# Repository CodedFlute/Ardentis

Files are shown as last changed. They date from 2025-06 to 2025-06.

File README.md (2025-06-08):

# Ardentis

> **⚠ WARNING:** This is currently a work in progress and untested. Only fly if you are willing and able to take full responsibility for any damage or property loss that may result from failure of this flight computer to operate as designed.

Ardentis is the best value high-performance flight computer designed specifically for high-power rocketry at all levels from 38mm min diameter to 132mm dual stage space shots.

This repository contains both the hardware and software required for Ardentis and its upgrades.

## Features

Ardentis comes in one default configurations, although any combination of features could be created by due to its open source design philosophy.

| Feature | Capability |
|-|-|
| Max Altitude | Baro: 25 km (85k ft) GPS: 80 km (250k ft) |
| GPS Tracking | Yes |
| Max Radio Range | ~15 km |
| Max Acceleration | 400G |
| Outputs | 4 (Servo + Air Start Capable) |
| Data Logging | MicroSD |
| Wi-Fi | Configuration and Control |

### Ardentis

<details>
<summary>Hardware Details</summary>

- **MCU**: ESP32-S3-MINI-1-N4R2
  - 4 MB Flash
  - 384 KB ROM
  - 512 KB SRAM
  - Dual core Xtense 32 bit LX7 at up to 240 MHz
- **Radio**: seeed studio SX126x Breakout
  - 22 dBm TX Power
  - 915 MHz ISM Band
  - u.Fl Antenna Connector
- **IMU**: ICM
  - +/- 16G Accelerometer
  - +/- 2000 Deg/s Gyroscope
- **High G Accelerometer**:
  - 3 Axis
  - +/- 100, 200, 400G Ranges
- **Barometer**: MS5611
  - 10 cm Resolution
  - 10 mBar to 1 200 mBar Operating Range
- **GPS**: uBlox SAM-M10Q
  - 80 km (250k ft) Max Altitude
  - 500 m/s (1.45 Mach) Max Velocity
  - 4G Max Acceleration
- **Ignition Channels**4
- **Connectivity**: Bluetooth 5.0, Wi-Fi, Micro USB
- **Power**: 1S LiPo battery support (or anything between 2V and 5V)

</details>

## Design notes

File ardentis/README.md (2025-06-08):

# Hardware

This folder contains the KiCAD files for the Ardentis hardware. These were made using KiCAD 9.0.

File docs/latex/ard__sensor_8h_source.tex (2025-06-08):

\doxysection{ard\+\_\+sensor.\+h}
\hypertarget{ard__sensor_8h_source}{}\label{ard__sensor_8h_source}\index{main/ard\_sensor.h@{main/ard\_sensor.h}}

\begin{DoxyCode}{0}
\DoxyCodeLine{00001\ \textcolor{preprocessor}{\#pragma\ once}}
\DoxyCodeLine{00002\ }
\DoxyCodeLine{00003\ \textcolor{preprocessor}{\#include\ <stdint.h>}}
\DoxyCodeLine{00004\ }
\DoxyCodeLine{00005\ \textcolor{preprocessor}{\#include\ <SparkFun\_u-\/blox\_GNSS\_v3.h>}}
\DoxyCodeLine{00006\ }
\DoxyCodeLine{00007\ \textcolor{preprocessor}{\#include\ <Adafruit\_Sensor.h>}\ \textcolor{comment}{//Needed\ for\ adafruit\ sensor\ libraries}}
\DoxyCodeLine{00008\ \textcolor{preprocessor}{\#include\ <Adafruit\_H3LIS331.h>}\ \textcolor{comment}{//\ For\ H3LIS331\ High\ G\ Accelerometer}}
\DoxyCodeLine{00009\ }
\DoxyCodeLine{00010\ \textcolor{preprocessor}{\#include\ <ICM42670P.h>}\ \textcolor{comment}{//\ For\ ICM42670P\ IMU}}
\DoxyCodeLine{00011\ }
\DoxyCodeLine{00012\ \textcolor{preprocessor}{\#include\ <icm42670.h>}}
\DoxyCodeLine{00013\ }
\DoxyCodeLine{00014\ \textcolor{preprocessor}{\#include\ <MS5611.h>}\ \textcolor{comment}{//\ For\ MS5611\ Barometer}}
\DoxyCodeLine{00015\ }
\DoxyCodeLine{00016\ \textcolor{preprocessor}{\#include\ <Wire.h>}\ \textcolor{comment}{//\ For\ I2C\ communication}}
\DoxyCodeLine{00017\ }
\DoxyCodeLine{00018\ \textcolor{preprocessor}{\#include\ <HardwareSerial.h>}}
\DoxyCodeLine{00019\ }
\DoxyCodeLine{00020\ \textcolor{preprocessor}{\#include\ <driver/i2c\_master.h>}}
\DoxyCodeLine{00027\ \textcolor{keyword}{struct\ }\mbox{\hyperlink{structard_data_field}{ardDataField}}\ \{}
\DoxyCodeLine{00028\ \ \ \ \ int16\_t\ val;}
\DoxyCodeLine{00029\ \ \ \ \ int64\_t\ timestamp;}
\DoxyCodeLine{00030\ \ \ \ \ \textcolor{keywordtype}{bool}\ updated;}
\DoxyCodeLine{00031\ \};}
\DoxyCodeLine{00037\ \textcolor{keywordtype}{void}\ updateArdDataField(\mbox{\hyperlink{structard_data_field}{ardDataField}}*\ field,\ int16\_t\ val);}
\DoxyCodeLine{00038\ }
\DoxyCodeLine{00048\ \textcolor{keyword}{class\ }ardSensors\ \{}
\DoxyCodeLine{00049\ \textcolor{keyword}{public}:}
\DoxyCodeLine{00050\ \ \ \ \ ardSensors(gpio\_num\_t\ sda,\ gpio\_num\_t\ scl,\ \textcolor{keywordtype}{int}\ i2c,\ \textcolor{keywordtype}{int}\ gps\_uart\_num,\ gpio\_num\_t\ gps\_tx,\ gpio\_num\_t\ gps\_rx);}
\DoxyCodeLine{00051\ \ \ \ \ \string~ardSensors();}
\DoxyCodeLine{00052\ }
\DoxyCodeLine{00061\ \ \ \ \ esp\_err\_t\ \mbox{\hyperlink{classard_sensors_af8da5ef8f7232141c86709f8613ad1a3}{initSensors}}(\textcolor{keywordtype}{int}\ LIS331\_addr,\ \textcolor{keywordtype}{int}\ imu\_adr,\ \textcolor{keywordtype}{int}\ baro\_addr,\ \textcolor{keywordtype}{int}\ gps\_baud);}
\DoxyCodeLine{00062\ \ \ \ \ esp\_err\_t\ update();\ \textcolor{comment}{//\ Function\ to\ check\ if\ new\ sensor\ data\ is\ available\ and\ update\ the\ data\ fields\ accordingly.}}
\DoxyCodeLine{00063\ \ \ \ \ \mbox{\hyperlink{structard_data_field}{ardDataField}}\ accelX;\ \textcolor{comment}{//\ Accelerometer\ X-\/axis\ data}}
\DoxyCodeLine{00064\ \ \ \ \ \mbox{\hyperlink{structard_data_field}{ardDataField}}\ accelY;\ \textcolor{comment}{//\ Accelerometer\ Y-\/axis\ data}}
\DoxyCodeLine{00065\ \ \ \ \ \mbox{\hyperlink{structard_data_field}{ardDataField}}\ accelZ;\ \textcolor{comment}{//\ Accelerometer\ Z-\/axis\ data}}
\DoxyCodeLine{00066\ \ \ \ \ \mbox{\hyperlink{structard_data_field}{ardDataField}}\ gyroX;\ \textcolor{comment}{//\ Gyroscope\ X-\/axis\ data}}
\DoxyCodeLine{00067\ \ \ \ \ \mbox{\hyperlink{structard_data_field}{ardDataField}}\ gyroY;\ \textcolor{comment}{//\ Gyroscope\ Y-\/axis\ data}}
\DoxyCodeLine{00068\ \ \ \ \ \mbox{\hyperlink{structard_data_field}{ardDataField}}\ gyroZ;\ \textcolor{comment}{//\ Gyroscope\ Y-\/axis\ data}}
\DoxyCodeLine{00069\ \ \ \ \ \mbox{\hyperlink{structard_data_field}{ardDataField}}\ highAccelX;\ \textcolor{comment}{//\ High\ G\ Accelerometer\ X-\/axis\ data}}
\DoxyCodeLine{00070\ \ \ \ \ \mbox{\hyperlink{structard_data_field}{ardDataField}}\ highAccelY;\ \textcolor{comment}{//\ High\ G\ Accelerometer\ Y-\/axis\ data}}
\DoxyCodeLine{00071\ \ \ \ \ \mbox{\hyperlink{structard_data_field}{ardDataField}}\ highAccelZ;\ \textcolor{comment}{//\ High\ G\ Accelerometer\ Z-\/axis\ data}}
\DoxyCodeLine{00072\ \ \ \ \ \mbox{\hyperlink{structard_data_field}{ardDataField}}\ pressure;\ \textcolor{comment}{//\ Pressure\ data\ from\ barometer}}
\DoxyCodeLine{00073\ \ \ \ \ \mbox{\hyperlink{structard_data_field}{ardDataField}}\ altitude;\ \textcolor{comment}{//\ Altitude\ data\ from\ barometer}}
\DoxyCodeLine{00074\ \ \ \ \ \mbox{\hyperlink{structard_data_field}{ardDataField}}\ temperature;\ \textcolor{comment}{//\ Temperature\ data\ from\ barometer}}
\DoxyCodeLine{00075\ \ \ \ \ \mbox{\hyperlink{structard_data_field}{ardDataField}}\ latitude;\ \textcolor{comment}{//\ Latitude\ data\ from\ GPS}}
\DoxyCodeLine{00076\ \ \ \ \ \mbox{\hyperlink{structard_data_field}{ardDataField}}\ longitude;\ \textcolor{comment}{//\ Longitude\ data\ from\ GPS}}
\DoxyCodeLine{00077\ \ \ \ \ \mbox{\hyperlink{structard_data_field}{ardDataField}}\ horizAccuracy;\ \textcolor{comment}{//\ Horizontal\ accuracy\ from\ GPS}}
\DoxyCodeLine{00078\ \ \ \ \ \mbox{\hyperlink{structard_data_field}{ardDataField}}\ vertAccuracy;\ \textcolor{comment}{//\ Vertical\ accuracy\ from\ GPS}}
\DoxyCodeLine{00079\ \ \ \ \ \mbox{\hyperlink{structard_data_field}{ardDataField}}\ gps\_altitude;\ \textcolor{comment}{//\ Altitude\ data\ from\ GPS}}
\DoxyCodeLine{00080\ \textcolor{keyword}{private}:}
\DoxyCodeLine{00081\ \ \ \ \ TwoWire\ ard\_sensor\_i2c\ =\ NULL;\ \textcolor{comment}{//\ Arduino\ I2C\ bus\ object}}
\DoxyCodeLine{00082\ \ \ \ \ SFE\_UBLOX\_GNSS\_SERIAL\ gps;\ \textcolor{comment}{//\ GPS\ object}}
\DoxyCodeLine{00083\ \ \ \ \ HardwareSerial\ gps\_uart\ =\ NULL;\ \textcolor{comment}{//\ GPS\ UART\ bus\ object}}
\DoxyCodeLine{00084\ \ \ \ \ MS5611\ barometer;\ \textcolor{comment}{//\ Barometer\ object}}
\DoxyCodeLine{00085\ \ \ \ \ Adafruit\_H3LIS331\ accel\ =\ Adafruit\_H3LIS331();\ \textcolor{comment}{//\ High\ G\ Accelerometer\ object}}
\DoxyCodeLine{00086\ \ \ \ \ icm42670\_handle\_t\ imu\_handle\ =\ \textcolor{keyword}{nullptr};\ \textcolor{comment}{//\ ICM42670\ IMU\ object}}
\DoxyCodeLine{00087\ \ \ \ \ i2c\_master\_bus\_handle\_t\ i2c\_handle\ =\ NULL;\ \textcolor{comment}{//\ ESP-\/IDF\ I2C\ bus\ object}}
\DoxyCodeLine{00088\ \ \ \ \ gpio\_num\_t\ sda;\ \textcolor{comment}{//\ SDA\ GPIO\ pin}}
\DoxyCodeLine{00089\ \ \ \ \ gpio\_num\_t\ scl;\ \textcolor{comment}{//\ SCL\ GPIO\ pin}}
\DoxyCodeLine{00090\ \ \ \ \ gpio\_num\_t\ uart\_rx;\ \textcolor{comment}{//\ GPS\ RX\ GPIO\ pin}}
\DoxyCodeLine{00091\ \ \ \ \ gpio\_num\_t\ uart\_tx;\ \textcolor{comment}{//\ GPS\ TX\ GPIO\ pin}}
\DoxyCodeLine{00092\ \ \ \ \ \textcolor{keywordtype}{int}\ gps\_uart\_num;\ \textcolor{comment}{//\ GPS\ UART\ bus\ number}}
\DoxyCodeLine{00093\ \ \ \ \ \textcolor{keywordtype}{int}\ i2c\_num;\ \textcolor{comment}{//\ I2C\ bus\ number}}
\DoxyCodeLine{00094\ \ \ \ \ int16\_t\ imu\_update\_time;\ \textcolor{comment}{//\ Timestamp\ of\ the\ last\ IMU\ update}}
\DoxyCodeLine{00095\ \ \ \ \ int16\_t\ imu\_update\_interval;\ \textcolor{comment}{//\ Interval\ between\ IMU\ updates\ in\ microseconds}}
\DoxyCodeLine{00096\ \ \ \ \ int16\_t\ high\_g\_accel\_update\_time;\ \textcolor{comment}{//\ Timestamp\ of\ the\ last\ High\ G\ Accelerometer\ update}}
\DoxyCodeLine{00097\ \ \ \ \ int16\_t\ high\_g\_accel\_update\_interval;\ \textcolor{comment}{//\ Interval\ between\ High\ G\ Accelerometer\ updates\ in\ microseconds}}
\DoxyCodeLine{00098\ \ \ \ \ int16\_t\ barometer\_update\_time;\ \textcolor{comment}{//\ Timestamp\ of\ the\ last\ Barometer\ update}}
\DoxyCodeLine{00099\ \ \ \ \ int16\_t\ barometer\_update\_interval;\ \textcolor{comment}{//\ Interval\ between\ Barometer\ updates\ in\ microseconds}}
\DoxyCodeLine{00100\ \ \ \ \ int16\_t\ gps\_update\_time;\ \textcolor{comment}{//\ Timestamp\ of\ the\ last\ GPS\ update}}
\DoxyCodeLine{00101\ \ \ \ \ int16\_t\ gps\_update\_interval;\ \textcolor{comment}{//\ Interval\ between\ GPS\ updates\ in\ microseconds}}
\DoxyCodeLine{00102\ \};}

\end{DoxyCode}

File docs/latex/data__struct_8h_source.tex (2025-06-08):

\doxysection{data\+\_\+struct.\+h}
\hypertarget{data__struct_8h_source}{}\label{data__struct_8h_source}\index{main/data\_struct.h@{main/data\_struct.h}}

\begin{DoxyCode}{0}
\DoxyCodeLine{00001\ \textcolor{preprocessor}{\#pragma\ once}}
\DoxyCodeLine{00002\ }
\DoxyCodeLine{00003\ \textcolor{preprocessor}{\#include\ <Arduino.h>}}
\DoxyCodeLine{00004\ }
\DoxyCodeLine{00005\ \textcolor{keyword}{struct\ }\mbox{\hyperlink{struct_ard_data_struct}{ArdDataStruct}}\ \{}
\DoxyCodeLine{00006\ \ \ \ \ uint16\_t\ pressure;}
\DoxyCodeLine{00007\ \ \ \ \ int32\_t\ latitude;}
\DoxyCodeLine{00008\ \ \ \ \ int32\_t\ longitude;}
\DoxyCodeLine{00009\ \ \ \ \ int16\_t\ horizAccuracy;}
\DoxyCodeLine{00010\ \ \ \ \ int16\_t\ vertAccuracy;}
\DoxyCodeLine{00011\ \ \ \ \ int16\_t\ temperature;}
\DoxyCodeLine{00012\ \ \ \ \ int16\_t\ accelX;}
\DoxyCodeLine{00013\ \ \ \ \ int16\_t\ accelY;}
\DoxyCodeLine{00014\ \ \ \ \ int16\_t\ accelZ;}
\DoxyCodeLine{00015\ \ \ \ \ int16\_t\ highAccelX;}
\DoxyCodeLine{00016\ \ \ \ \ int16\_t\ highAccelY;}
\DoxyCodeLine{00017\ \ \ \ \ int16\_t\ highAccelZ;}
\DoxyCodeLine{00018\ \ \ \ \ int16\_t\ gyroX;}
\DoxyCodeLine{00019\ \ \ \ \ int16\_t\ gyroY;}
\DoxyCodeLine{00020\ \ \ \ \ int16\_t\ gyroZ;}
\DoxyCodeLine{00021\ \ \ \ \ int16\_t\ altitude;}
\DoxyCodeLine{00022\ \ \ \ \ \textcolor{keywordtype}{bool}\ cont1;}
\DoxyCodeLine{00023\ \ \ \ \ \textcolor{keywordtype}{bool}\ cont2;}
\DoxyCodeLine{00024\ \ \ \ \ \textcolor{keywordtype}{bool}\ cont3;}
\DoxyCodeLine{00025\ \ \ \ \ \textcolor{keywordtype}{bool}\ cont4;}
\DoxyCodeLine{00026\ \ \ \ \ \textcolor{keywordtype}{bool}\ fired\_1;}
\DoxyCodeLine{00027\ \ \ \ \ \textcolor{keywordtype}{bool}\ fired\_2;}
\DoxyCodeLine{00028\ \ \ \ \ \textcolor{keywordtype}{bool}\ fired\_3;}
\DoxyCodeLine{00029\ \ \ \ \ \textcolor{keywordtype}{bool}\ fired\_4;}
\DoxyCodeLine{00030\ }
\DoxyCodeLine{00031\ \ \ \ \ uint16\_t\ getAltitude(\textcolor{keywordtype}{int}\ sea\_pressure)\textcolor{keyword}{\ const\ }\{}
\DoxyCodeLine{00032\ \ \ \ \ \ \ \ \ \textcolor{comment}{//\ Example\ calculation\ for\ altitude\ based\ on\ pressure}}
\DoxyCodeLine{00033\ \ \ \ \ \ \ \ \ \textcolor{comment}{//\ Replace\ with\ your\ actual\ formula}}
\DoxyCodeLine{00034\ \ \ \ \ \ \ \ \ \textcolor{keywordflow}{return}\ ((pow((sea\_pressure\ /\ pressure),\ 1/5.257)\ -\/\ 1.0)\ *\ (temperature\ +\ 273.15))\ /\ 0.0065;}
\DoxyCodeLine{00035\ \ \ \ \ \}}
\DoxyCodeLine{00036\ \};}

\end{DoxyCode}

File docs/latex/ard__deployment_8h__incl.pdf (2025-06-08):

main/ard_deployment.h

driver/gpio.h | esp_err.h | esp_log.h

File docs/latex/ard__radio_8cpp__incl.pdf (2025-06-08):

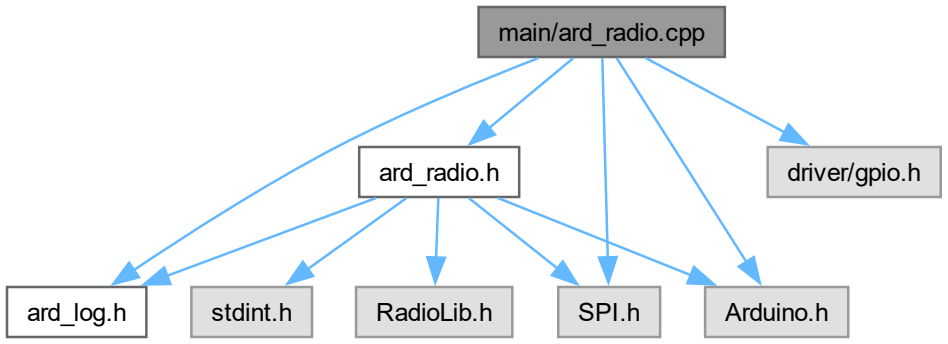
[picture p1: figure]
main/ard_radio.cpp; ard_radio.h; ard_log.h; SPI.h; Arduino.h; driver/gpio.h; stdint.h; RadioLib.h

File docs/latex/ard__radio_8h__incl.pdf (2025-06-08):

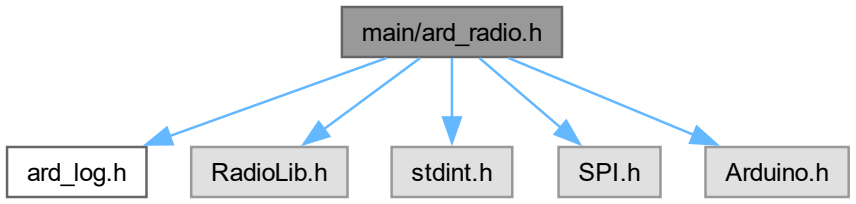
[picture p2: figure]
main/ard_radio.h; ard_log.h; RadioLib.h; stdint.h; SPI.h; Arduino.h

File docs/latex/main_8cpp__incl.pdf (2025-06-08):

main/main.cpp

pins.h

fire_modes.hpp | RadioParameters.h | ard_radio.h
ard_log.h | Arduino.h
data_struct.h | ard_deployment.h

Wire.h

FS.h | LittleFS.h | SD.h | Preferences.h | ard_sensor.h
RadioLib.h | SPI.h | driver/gpio.h | stdint.h | esp_err.h | esp_log.h | HardwareSerial.h | driver/i2c_master.h | SparkFun_u-blox_GNSS_v3.h | Adafruit_Sensor.h | Adafruit_H3LIS331.h | ICM42670P.h | icm42670.h | MS5611.h

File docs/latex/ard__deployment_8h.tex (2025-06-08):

\doxysection{main/ard\+\_\+deployment.h File Reference}
\hypertarget{ard__deployment_8h}{}\label{ard__deployment_8h}\index{main/ard\_deployment.h@{main/ard\_deployment.h}}

Header file for the ard\+\_\+deployment class.  

{\ttfamily \#include $<$driver/gpio.\+h$>$}\newline
{\ttfamily \#include $<$esp\+\_\+err.\+h$>$}\newline
{\ttfamily \#include $<$esp\+\_\+log.\+h$>$}\newline
Include dependency graph for ard\+\_\+deployment.\+h\+:\nopagebreak
\begin{figure}[H]
\begin{center}
\leavevmode

\end{center}
\end{figure}
This graph shows which files directly or indirectly include this file\+:\nopagebreak
\begin{figure}[H]
\begin{center}
\leavevmode

\end{center}
\end{figure}
\doxysubsubsection*{Classes}
\begin{DoxyCompactItemize}
\item 
struct \mbox{\hyperlink{structard_deploy_gpio_config}{ard\+Deploy\+Gpio\+Config}}
\begin{DoxyCompactList}\small\item\em Configuration structure for GPIO pins used in deployment. \end{DoxyCompactList}\item 
class \mbox{\hyperlink{classard_output_g_p_i_o}{ard\+Output\+GPIO}}
\begin{DoxyCompactList}\small\item\em Class to manage GPIO pins for deployment. \end{DoxyCompactList}\end{DoxyCompactItemize}
\doxysubsubsection*{Enumerations}
\begin{DoxyCompactItemize}
\item 
enum class \mbox{\hyperlink{ard__deployment_8h_a0d5bf0014cb0a1f121b08aef183dffc5}{Fire\+Pins}} \+: uint8\+\_\+t \{ {\bfseries Zero} = 0
, {\bfseries One} = 1
, {\bfseries Two} = 2
, {\bfseries Three} = 3
 \}
\begin{DoxyCompactList}\small\item\em Enum containing the valid fire indices. \end{DoxyCompactList}\end{DoxyCompactItemize}

\doxysubsection{Detailed Description}
Header file for the ard\+\_\+deployment class. 

\begin{DoxyAuthor}{Author}
Roland Neill 
\end{DoxyAuthor}
\begin{DoxyVersion}{Version}
0.\+1 
\end{DoxyVersion}
\begin{DoxyDate}{Date}
2025-\/04-\/25
\end{DoxyDate}
\begin{DoxyCopyright}{Copyright}
Copyright (c) 2025
\end{DoxyCopyright}
This file contains the definition of the ard\+\_\+deployment class, which is used to manage GPIO pins for deployment purposes. 

\doxysubsection{Enumeration Type Documentation}
\Hypertarget{ard__deployment_8h_a0d5bf0014cb0a1f121b08aef183dffc5}\index{ard\_deployment.h@{ard\_deployment.h}!FirePins@{FirePins}}
\index{FirePins@{FirePins}!ard\_deployment.h@{ard\_deployment.h}}
\doxysubsubsection{\texorpdfstring{FirePins}{FirePins}}
{\footnotesize\ttfamily \label{ard__deployment_8h_a0d5bf0014cb0a1f121b08aef183dffc5} 
enum class \mbox{\hyperlink{ard__deployment_8h_a0d5bf0014cb0a1f121b08aef183dffc5}{Fire\+Pins}} \+: uint8\+\_\+t\hspace{0.3cm}{\ttfamily [strong]}}

Enum containing the valid fire indices. 

\begin{DoxyCode}{0}
\DoxyCodeLine{00037\ \ \ \ \ \ \ \ \ \ \ \ \ \ \ \ \ \ \ \ \ :\ uint8\_t\ \{}
\DoxyCodeLine{00038\ \ \ \ \ Zero\ =\ 0,}
\DoxyCodeLine{00039\ \ \ \ \ One\ =\ 1,}
\DoxyCodeLine{00040\ \ \ \ \ Two\ =\ 2,}
\DoxyCodeLine{00041\ \ \ \ \ Three\ =\ 3}
\DoxyCodeLine{00042\ \};}

\end{DoxyCode}

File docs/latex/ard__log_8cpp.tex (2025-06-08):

\doxysection{main/ard\+\_\+log.cpp File Reference}
\hypertarget{ard__log_8cpp}{}\label{ard__log_8cpp}\index{main/ard\_log.cpp@{main/ard\_log.cpp}}

Logging library implementation for the Ardentis flight computer.  

{\ttfamily \#include "{}ard\+\_\+log.\+h"{}}\newline
{\ttfamily \#include $<$esp\+\_\+log.\+h$>$}\newline
Include dependency graph for ard\+\_\+log.\+cpp\+:
\nopagebreak
\begin{figure}[H]
\begin{center}
\leavevmode

\end{center}
\end{figure}

\doxysubsection{Detailed Description}
Logging library implementation for the Ardentis flight computer. 

\begin{DoxyAuthor}{Author}
Roland Neill 
\end{DoxyAuthor}
\begin{DoxyVersion}{Version}
0.\+1-\/alpha 
\end{DoxyVersion}
\begin{DoxyDate}{Date}
2025-\/04-\/28
\end{DoxyDate}
\begin{DoxyCopyright}{Copyright}
Copyright (c) 2025 
\end{DoxyCopyright}

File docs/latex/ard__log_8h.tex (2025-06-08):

\doxysection{main/ard\+\_\+log.h File Reference}
\hypertarget{ard__log_8h}{}\label{ard__log_8h}\index{main/ard\_log.h@{main/ard\_log.h}}

Logging library header for the Ardentis flight computer.  

This graph shows which files directly or indirectly include this file\+:
\nopagebreak
\begin{figure}[H]
\begin{center}
\leavevmode
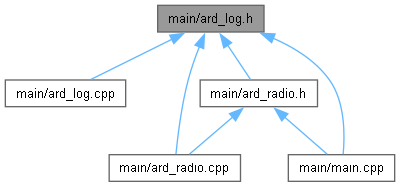
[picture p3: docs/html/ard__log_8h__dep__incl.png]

\end{center}
\end{figure}
\doxysubsubsection*{Classes}
\begin{DoxyCompactItemize}
\item 
class \mbox{\hyperlink{classard_log}{ard\+Log}}
\end{DoxyCompactItemize}
\doxysubsubsection*{Enumerations}
\begin{DoxyCompactItemize}
\item 
enum \mbox{\hyperlink{ard__log_8h_a2bcec6abac24273ae7d38f257f7d41b4}{ard\+\_\+log\+Level\+\_\+t}} \{ \newline
{\bfseries LOG\+\_\+\+DISABLE} = 0
, {\bfseries LOG\+\_\+\+ERROR} = 1
, {\bfseries LOG\+\_\+\+WARN} = 2
, {\bfseries LOG\+\_\+\+INFO} = 3
, \newline
{\bfseries LOG\+\_\+\+DEBUG} = 4
, {\bfseries LOG\+\_\+\+VERBOSE} = 5
 \}
\begin{DoxyCompactList}\small\item\em Logging level enum type. \end{DoxyCompactList}\item 
enum \mbox{\hyperlink{ard__log_8h_ab24eeb30e1bc9136bb3054df8c6e1470}{ard\+\_\+error\+Code\+\_\+t}} \{ {\bfseries ERROR\+\_\+\+NONE} = 0
, {\bfseries ERROR\+\_\+\+GENERIC} = -\/1
 \}
\begin{DoxyCompactList}\small\item\em Enumeration type for error codes. \end{DoxyCompactList}\end{DoxyCompactItemize}

\doxysubsection{Detailed Description}
Logging library header for the Ardentis flight computer. 

\begin{DoxyAuthor}{Author}
Roland Neill 
\end{DoxyAuthor}
\begin{DoxyVersion}{Version}
0.\+1-\/alpha 
\end{DoxyVersion}
\begin{DoxyDate}{Date}
2025-\/04-\/28
\end{DoxyDate}
\begin{DoxyCopyright}{Copyright}
Copyright (c) 2025 
\end{DoxyCopyright}

\doxysubsection{Enumeration Type Documentation}
\Hypertarget{ard__log_8h_ab24eeb30e1bc9136bb3054df8c6e1470}\index{ard\_log.h@{ard\_log.h}!ard\_errorCode\_t@{ard\_errorCode\_t}}
\index{ard\_errorCode\_t@{ard\_errorCode\_t}!ard\_log.h@{ard\_log.h}}
\doxysubsubsection{\texorpdfstring{ard\_errorCode\_t}{ard\_errorCode\_t}}
{\footnotesize\ttfamily \label{ard__log_8h_ab24eeb30e1bc9136bb3054df8c6e1470} 
enum \mbox{\hyperlink{ard__log_8h_ab24eeb30e1bc9136bb3054df8c6e1470}{ard\+\_\+error\+Code\+\_\+t}}}

Enumeration type for error codes. 

\begin{DoxyCode}{0}
\DoxyCodeLine{00030\ \ \ \ \ \ \ \ \ \ \ \ \ \ \ \ \ \ \ \ \ \ \{}
\DoxyCodeLine{00031\ \ \ \ \ ERROR\_NONE\ =\ 0,}
\DoxyCodeLine{00032\ \ \ \ \ ERROR\_GENERIC\ =\ -\/1}
\DoxyCodeLine{00033\ \};}

\end{DoxyCode}
\Hypertarget{ard__log_8h_a2bcec6abac24273ae7d38f257f7d41b4}\index{ard\_log.h@{ard\_log.h}!ard\_logLevel\_t@{ard\_logLevel\_t}}
\index{ard\_logLevel\_t@{ard\_logLevel\_t}!ard\_log.h@{ard\_log.h}}
\doxysubsubsection{\texorpdfstring{ard\_logLevel\_t}{ard\_logLevel\_t}}
{\footnotesize\ttfamily \label{ard__log_8h_a2bcec6abac24273ae7d38f257f7d41b4} 
enum \mbox{\hyperlink{ard__log_8h_a2bcec6abac24273ae7d38f257f7d41b4}{ard\+\_\+log\+Level\+\_\+t}}}

Logging level enum type. 

\begin{DoxyCode}{0}
\DoxyCodeLine{00017\ \ \ \ \ \ \ \ \ \ \ \ \ \ \ \ \ \ \ \ \ \{}
\DoxyCodeLine{00018\ \ \ \ \ LOG\_DISABLE\ =\ 0,}
\DoxyCodeLine{00019\ \ \ \ \ LOG\_ERROR\ =\ 1,}
\DoxyCodeLine{00020\ \ \ \ \ LOG\_WARN\ =\ 2,}
\DoxyCodeLine{00021\ \ \ \ \ LOG\_INFO\ =\ 3,}
\DoxyCodeLine{00022\ \ \ \ \ LOG\_DEBUG\ =\ 4,}
\DoxyCodeLine{00023\ \ \ \ \ LOG\_VERBOSE\ =\ 5}
\DoxyCodeLine{00024\ \};}

\end{DoxyCode}

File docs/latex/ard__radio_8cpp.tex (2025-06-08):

\doxysection{main/ard\+\_\+radio.cpp File Reference}
\hypertarget{ard__radio_8cpp}{}\label{ard__radio_8cpp}\index{main/ard\_radio.cpp@{main/ard\_radio.cpp}}

Implementation code for the radio module for the Ardentis flight computer.  

{\ttfamily \#include "{}ard\+\_\+radio.\+h"{}}\newline
{\ttfamily \#include "{}ard\+\_\+log.\+h"{}}\newline
{\ttfamily \#include "{}driver/gpio.\+h"{}}\newline
{\ttfamily \#include $<$Arduino.\+h$>$}\newline
{\ttfamily \#include $<$SPI.\+h$>$}\newline
Include dependency graph for ard\+\_\+radio.\+cpp\+:
\nopagebreak
\begin{figure}[H]
\begin{center}
\leavevmode
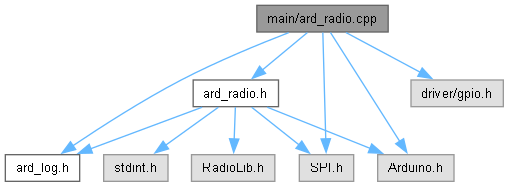
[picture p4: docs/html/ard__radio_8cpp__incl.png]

\end{center}
\end{figure}
\doxysubsubsection*{Functions}
\begin{DoxyCompactItemize}
\item 
byte \texorpdfstring{$\ast$}{*} \mbox{\hyperlink{ard__radio_8cpp_a4f22a60691cf95391c78bf6419803ade}{encode\+Packet}} (\mbox{\hyperlink{struct_radio_packet}{Radio\+Packet}} packet)
\end{DoxyCompactItemize}
\doxysubsubsection*{Variables}
\begin{DoxyCompactItemize}
\item 
\Hypertarget{ard__radio_8cpp_a13157ab59478a2cf89d8a25abfc1457e}\label{ard__radio_8cpp_a13157ab59478a2cf89d8a25abfc1457e} 
const char \texorpdfstring{$\ast$}{*} {\bfseries radio\+\_\+\+TAG} = "{}Radio"{}
\item 
\Hypertarget{ard__radio_8cpp_a168969af9060c19b152bebc14be89779}\label{ard__radio_8cpp_a168969af9060c19b152bebc14be89779} 
\mbox{\hyperlink{classard_log}{ard\+Log}} {\bfseries radio\+\_\+log} (radio\+\_\+\+TAG)
\end{DoxyCompactItemize}

\doxysubsection{Detailed Description}
Implementation code for the radio module for the Ardentis flight computer. 

\begin{DoxyAuthor}{Author}
Roland Neill 
\end{DoxyAuthor}
\begin{DoxyVersion}{Version}
0.\+1-\/alpha 
\end{DoxyVersion}
\begin{DoxyDate}{Date}
2025-\/04-\/28
\end{DoxyDate}
\begin{DoxyCopyright}{Copyright}
Copyright (c) 2025 
\end{DoxyCopyright}

\doxysubsection{Function Documentation}
\Hypertarget{ard__radio_8cpp_a4f22a60691cf95391c78bf6419803ade}\index{ard\_radio.cpp@{ard\_radio.cpp}!encodePacket@{encodePacket}}
\index{encodePacket@{encodePacket}!ard\_radio.cpp@{ard\_radio.cpp}}
\doxysubsubsection{\texorpdfstring{encodePacket()}{encodePacket()}}
{\footnotesize\ttfamily \label{ard__radio_8cpp_a4f22a60691cf95391c78bf6419803ade} 
byte \texorpdfstring{$\ast$}{*} encode\+Packet (\begin{DoxyParamCaption}\item[{\mbox{\hyperlink{struct_radio_packet}{Radio\+Packet}}}]{packet}{}\end{DoxyParamCaption})}

\begin{DoxyCode}{0}
\DoxyCodeLine{00026\ \ \ \ \ \ \ \ \ \ \ \ \ \ \ \ \ \ \ \ \ \ \ \ \ \ \ \ \ \ \ \ \ \ \ \ \ \ \ \ \{}
\DoxyCodeLine{00027\ \ \ \ \ \textcolor{keywordtype}{byte}*\ encodedData\ =\ \textcolor{keyword}{new}\ \textcolor{keywordtype}{byte}[16];}
\DoxyCodeLine{00028\ \ \ \ \ encodedData[0]\ =\ packet.callsign[0];}
\DoxyCodeLine{00029\ \ \ \ \ encodedData[1]\ =\ packet.callsign[1];}
\DoxyCodeLine{00030\ \ \ \ \ encodedData[2]\ =\ packet.callsign[2];}
\DoxyCodeLine{00031\ \ \ \ \ encodedData[3]\ =\ packet.callsign[3];}
\DoxyCodeLine{00032\ \ \ \ \ encodedData[4]\ =\ packet.callsign[4];}
\DoxyCodeLine{00033\ \ \ \ \ encodedData[5]\ =\ uint8\_t(0);\ \textcolor{comment}{//\ Packet\ Version\ number}}
\DoxyCodeLine{00034\ \ \ \ \ encodedData[6]\ =\ uint8\_t(packet.latitude\ >>\ 24);}
\DoxyCodeLine{00035\ \ \ \ \ encodedData[7]\ =\ uint8\_t(packet.latitude\ >>\ 16);}
\DoxyCodeLine{00036\ \ \ \ \ encodedData[8]\ =\ uint8\_t(packet.latitude\ >>\ 8);}
\DoxyCodeLine{00037\ \ \ \ \ encodedData[9]\ =\ uint8\_t(packet.latitude);}
\DoxyCodeLine{00038\ \ \ \ \ encodedData[10]\ =\ uint8\_t(packet.longitude\ >>\ 24);}
\DoxyCodeLine{00039\ \ \ \ \ encodedData[11]\ =\ uint8\_t(packet.longitude\ >>\ 16);}
\DoxyCodeLine{00040\ \ \ \ \ encodedData[12]\ =\ uint8\_t(packet.longitude\ >>\ 8);}
\DoxyCodeLine{00041\ \ \ \ \ encodedData[13]\ =\ uint8\_t(packet.longitude);}
\DoxyCodeLine{00042\ \ \ \ \ encodedData[14]\ =\ uint8\_t(packet.altitude\ >>\ 8);}
\DoxyCodeLine{00043\ \ \ \ \ encodedData[15]\ =\ uint8\_t(packet.altitude);}
\DoxyCodeLine{00044\ \ \ \ \ \textcolor{keywordflow}{return}\ encodedData;}
\DoxyCodeLine{00045\ \}}

\end{DoxyCode}

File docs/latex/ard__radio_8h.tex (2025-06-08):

\doxysection{main/ard\+\_\+radio.h File Reference}
\hypertarget{ard__radio_8h}{}\label{ard__radio_8h}\index{main/ard\_radio.h@{main/ard\_radio.h}}
{\ttfamily \#include "{}ard\+\_\+log.\+h"{}}\newline
{\ttfamily \#include $<$Radio\+Lib.\+h$>$}\newline
{\ttfamily \#include $<$stdint.\+h$>$}\newline
{\ttfamily \#include $<$SPI.\+h$>$}\newline
{\ttfamily \#include $<$Arduino.\+h$>$}\newline
Include dependency graph for ard\+\_\+radio.\+h\+:
\nopagebreak
\begin{figure}[H]
\begin{center}
\leavevmode

\end{center}
\end{figure}
This graph shows which files directly or indirectly include this file\+:
\nopagebreak
\begin{figure}[H]
\begin{center}
\leavevmode

\end{center}
\end{figure}
\doxysubsubsection*{Classes}
\begin{DoxyCompactItemize}
\item 
struct \mbox{\hyperlink{struct_radio_packet}{Radio\+Packet}}
\item 
struct \mbox{\hyperlink{structard___radio_config__t}{ard\+\_\+\+Radio\+Config\+\_\+t}}
\begin{DoxyCompactList}\small\item\em Structure to hold the Lo\+Ra configuration parameters. \end{DoxyCompactList}\item 
struct \mbox{\hyperlink{structard___radio_pins__t}{ard\+\_\+\+Radio\+Pins\+\_\+t}}
\begin{DoxyCompactList}\small\item\em Structure to hold the radio pin configuration parameters. \end{DoxyCompactList}\item 
class \mbox{\hyperlink{classard_radio}{ard\+Radio}}
\end{DoxyCompactItemize}
\doxysubsubsection*{Functions}
\begin{DoxyCompactItemize}
\item 
byte \texorpdfstring{$\ast$}{*} \mbox{\hyperlink{ard__radio_8h_a4f22a60691cf95391c78bf6419803ade}{encode\+Packet}} (\mbox{\hyperlink{struct_radio_packet}{Radio\+Packet}} packet)
\item 
\Hypertarget{ard__radio_8h_aab4e1dda370fc840688805541c6f7816}\label{ard__radio_8h_aab4e1dda370fc840688805541c6f7816} 
\mbox{\hyperlink{struct_radio_packet}{Radio\+Packet}} {\bfseries decode\+Packet} (byte data\mbox{[}18\mbox{]}, int length)
\end{DoxyCompactItemize}

\doxysubsection{Detailed Description}
\begin{DoxyAuthor}{Author}
Roland Neill 
\end{DoxyAuthor}
\begin{DoxyVersion}{Version}
0.\+1-\/alpha 
\end{DoxyVersion}
\begin{DoxyDate}{Date}
2025-\/04-\/28
\end{DoxyDate}
\begin{DoxyCopyright}{Copyright}
Copyright (c) 2025 
\end{DoxyCopyright}

\doxysubsection{Function Documentation}
\Hypertarget{ard__radio_8h_a4f22a60691cf95391c78bf6419803ade}\index{ard\_radio.h@{ard\_radio.h}!encodePacket@{encodePacket}}
\index{encodePacket@{encodePacket}!ard\_radio.h@{ard\_radio.h}}
\doxysubsubsection{\texorpdfstring{encodePacket()}{encodePacket()}}
{\footnotesize\ttfamily \label{ard__radio_8h_a4f22a60691cf95391c78bf6419803ade} 
byte \texorpdfstring{$\ast$}{*} encode\+Packet (\begin{DoxyParamCaption}\item[{\mbox{\hyperlink{struct_radio_packet}{Radio\+Packet}}}]{packet}{}\end{DoxyParamCaption})}

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

\end{DoxyCode}

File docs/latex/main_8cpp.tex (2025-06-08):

\doxysection{main/main.cpp File Reference}
\hypertarget{main_8cpp}{}\label{main_8cpp}\index{main/main.cpp@{main/main.cpp}}

Main file for the Ardentis flight computer code.  

{\ttfamily \#include "{}pins.\+h"{}}\newline
{\ttfamily \#include "{}fire\+\_\+modes.\+hpp"{}}\newline
{\ttfamily \#include "{}Radio\+Parameters.\+h"{}}\newline
{\ttfamily \#include "{}ard\+\_\+radio.\+h"{}}\newline
{\ttfamily \#include "{}data\+\_\+struct.\+h"{}}\newline
{\ttfamily \#include "{}ard\+\_\+deployment.\+h"{}}\newline
{\ttfamily \#include "{}ard\+\_\+log.\+h"{}}\newline
{\ttfamily \#include $<$Arduino.\+h$>$}\newline
{\ttfamily \#include $<$Wire.\+h$>$}\newline
{\ttfamily \#include $<$FS.\+h$>$}\newline
{\ttfamily \#include $<$Little\+FS.\+h$>$}\newline
{\ttfamily \#include $<$SD.\+h$>$}\newline
{\ttfamily \#include $<$Preferences.\+h$>$}\newline
{\ttfamily \#include "{}ard\+\_\+sensor.\+h"{}}\newline
Include dependency graph for main.\+cpp\+:
\nopagebreak
\begin{figure}[H]
\begin{center}
\leavevmode

\end{center}
\end{figure}
\doxysubsubsection*{Functions}
\begin{DoxyCompactItemize}
\item 
void \mbox{\hyperlink{main_8cpp_a94b7c389e4d61e6c9d8d34356c7919e8}{tx\+Callback}} (void)
\item 
void \mbox{\hyperlink{main_8cpp_a7dfd9b79bc5a37d7df40207afbc5431f}{setup}} (void)
\item 
void \mbox{\hyperlink{main_8cpp_afe461d27b9c48d5921c00d521181f12f}{loop}} ()
\end{DoxyCompactItemize}
\doxysubsubsection*{Variables}
\begin{DoxyCompactItemize}
\item 
\mbox{\hyperlink{structard___radio_config__t}{ard\+\_\+\+Radio\+Config\+\_\+t}} \mbox{\hyperlink{main_8cpp_ae75c26b3f0347f4abceb163265d2faf4}{radio\+Config}}
\item 
\mbox{\hyperlink{structard___radio_pins__t}{ard\+\_\+\+Radio\+Pins\+\_\+t}} \mbox{\hyperlink{main_8cpp_a52c567d1d8398c2a5f2574ccd2ab895a}{radio\+Pins}}
\item 
\Hypertarget{main_8cpp_a77cac75281a97328ac564439a9b0cf8b}\label{main_8cpp_a77cac75281a97328ac564439a9b0cf8b} 
\mbox{\hyperlink{classard_radio}{ard\+Radio}} {\bfseries radio} (radio\+Pins)
\item 
\Hypertarget{main_8cpp_aad04a79c69ec7291bddad0a204786f01}\label{main_8cpp_aad04a79c69ec7291bddad0a204786f01} 
const char \texorpdfstring{$\ast$}{*} {\bfseries main\+\_\+\+TAG} = "{}Main"{}
\item 
\Hypertarget{main_8cpp_ae2010c70c13130ab37e62d54d19845a8}\label{main_8cpp_ae2010c70c13130ab37e62d54d19845a8} 
\mbox{\hyperlink{classard_log}{ard\+Log}} {\bfseries main\+\_\+log} (main\+\_\+\+TAG)
\item 
\Hypertarget{main_8cpp_a0c701261da8421398e78be7f85026d00}\label{main_8cpp_a0c701261da8421398e78be7f85026d00} 
\mbox{\hyperlink{classard_sensors}{ard\+Sensors}} {\bfseries sensors} (ARD\+\_\+\+SDA, ARD\+\_\+\+SCL, 1, ARD\+\_\+\+GPS\+\_\+\+UART, ARD\+\_\+\+GPS\+\_\+\+TX, ARD\+\_\+\+GPS\+\_\+\+RX)
\item 
\Hypertarget{main_8cpp_a73eb8317f42311b30515bf4012193359}\label{main_8cpp_a73eb8317f42311b30515bf4012193359} 
File {\bfseries flight\+Log}
\item 
\Hypertarget{main_8cpp_a7c230fb3ef401aa42442d542049509f7}\label{main_8cpp_a7c230fb3ef401aa42442d542049509f7} 
bool {\bfseries fire\+\_\+signal\+\_\+1} = false
\item 
\Hypertarget{main_8cpp_ae32a1f12a67abae03c91b6fd0479cda8}\label{main_8cpp_ae32a1f12a67abae03c91b6fd0479cda8} 
bool {\bfseries fire\+\_\+signal\+\_\+2} = false
\item 
\Hypertarget{main_8cpp_afc17a94162fa06098708ed8d5ee6bbbb}\label{main_8cpp_afc17a94162fa06098708ed8d5ee6bbbb} 
bool {\bfseries fire\+\_\+signal\+\_\+3} = false
\item 
\Hypertarget{main_8cpp_aea251a0c4b89c2c59db708729e85a291}\label{main_8cpp_aea251a0c4b89c2c59db708729e85a291} 
bool {\bfseries fire\+\_\+signal\+\_\+4} = false
\item 
\Hypertarget{main_8cpp_a0f1c1cf688b55f3ba4a040ec13639f54}\label{main_8cpp_a0f1c1cf688b55f3ba4a040ec13639f54} 
bool {\bfseries continuity\+\_\+1} = false
\item 
\Hypertarget{main_8cpp_a0fd7d48fd0bf9155099ea51ba4eb4e94}\label{main_8cpp_a0fd7d48fd0bf9155099ea51ba4eb4e94} 
bool {\bfseries continuity\+\_\+2} = false
\item 
\Hypertarget{main_8cpp_ab703c208b47706aad98bdf1a85634883}\label{main_8cpp_ab703c208b47706aad98bdf1a85634883} 
bool {\bfseries continuity\+\_\+3} = false
\item 
\Hypertarget{main_8cpp_a86106782c4af95724364d1ba028722bf}\label{main_8cpp_a86106782c4af95724364d1ba028722bf} 
bool {\bfseries continuity\+\_\+4} = false
\item 
\Hypertarget{main_8cpp_a732fb02924cb0e2218d5094c2c5fc545}\label{main_8cpp_a732fb02924cb0e2218d5094c2c5fc545} 
bool {\bfseries apogee} = false
\item 
\Hypertarget{main_8cpp_a69cdbf327e1ec7ae957b431b74d5e932}\label{main_8cpp_a69cdbf327e1ec7ae957b431b74d5e932} 
uint16\+\_\+t {\bfseries time\+\_\+since\+\_\+apogee} = 0
\item 
\Hypertarget{main_8cpp_a51661d189e8db74a32867069dfa50d7f}\label{main_8cpp_a51661d189e8db74a32867069dfa50d7f} 
uint16\+\_\+t {\bfseries altitude} = 0
\item 
\Hypertarget{main_8cpp_adb7c0c50ea3a213314dcda50d70e65b3}\label{main_8cpp_adb7c0c50ea3a213314dcda50d70e65b3} 
bool {\bfseries descending} = false
\item 
\Hypertarget{main_8cpp_a8ea27602bf4d3ec3850549a2d313ad0c}\label{main_8cpp_a8ea27602bf4d3ec3850549a2d313ad0c} 
bool {\bfseries ascending} = false
\item 
\Hypertarget{main_8cpp_af477912513bde2ceb50583d4ace50e23}\label{main_8cpp_af477912513bde2ceb50583d4ace50e23} 
uint16\+\_\+t {\bfseries time\+\_\+since\+\_\+liftoff} = 0
\item 
\Hypertarget{main_8cpp_ada4b0d2294a1480cf9330b45bb5752f0}\label{main_8cpp_ada4b0d2294a1480cf9330b45bb5752f0} 
int {\bfseries ref\+\_\+pressure} = 101325
\item 
\Hypertarget{main_8cpp_addd29491336bdb1ec1269ace1921f2db}\label{main_8cpp_addd29491336bdb1ec1269ace1921f2db} 
uint8\+\_\+t {\bfseries fire\+\_\+1\+\_\+mode} = ARD\+\_\+\+FIRE\+\_\+\+INACTIVE
\item 
\Hypertarget{main_8cpp_a086adec30975fe9cccf45d567699a616}\label{main_8cpp_a086adec30975fe9cccf45d567699a616} 
uint8\+\_\+t {\bfseries fire\+\_\+1\+\_\+param} = 0
\item 
\Hypertarget{main_8cpp_a7f0e5c0d7dac8a71f9e4bcb3d883402e}\label{main_8cpp_a7f0e5c0d7dac8a71f9e4bcb3d883402e} 
uint8\+\_\+t {\bfseries fire\+\_\+2\+\_\+mode} = ARD\+\_\+\+FIRE\+\_\+\+INACTIVE
\item 
\Hypertarget{main_8cpp_a0d25b4249b97db6a9294d6f499f28dd8}\label{main_8cpp_a0d25b4249b97db6a9294d6f499f28dd8} 
uint8\+\_\+t {\bfseries fire\+\_\+2\+\_\+param} = 0
\item 
\Hypertarget{main_8cpp_a24e87c1bede4601685101da8ee550b3d}\label{main_8cpp_a24e87c1bede4601685101da8ee550b3d} 
uint8\+\_\+t {\bfseries fire\+\_\+3\+\_\+mode} = ARD\+\_\+\+FIRE\+\_\+\+INACTIVE
\item 
\Hypertarget{main_8cpp_a315be1fc037d6584940728a102a34132}\label{main_8cpp_a315be1fc037d6584940728a102a34132} 
uint8\+\_\+t {\bfseries fire\+\_\+3\+\_\+param} = 0
\item 
\Hypertarget{main_8cpp_ad909b603d34e2fb4376f3131b0376c27}\label{main_8cpp_ad909b603d34e2fb4376f3131b0376c27} 
uint8\+\_\+t {\bfseries fire\+\_\+4\+\_\+mode} = ARD\+\_\+\+FIRE\+\_\+\+INACTIVE
\item 
\Hypertarget{main_8cpp_a9d2d87aec547e136613b10f595686e15}\label{main_8cpp_a9d2d87aec547e136613b10f595686e15} 
uint8\+\_\+t {\bfseries fire\+\_\+4\+\_\+param} = 0
\item 
\Hypertarget{main_8cpp_a0e69f178b7968bba4c71ffd2534917d2}\label{main_8cpp_a0e69f178b7968bba4c71ffd2534917d2} 
uint8\+\_\+t {\bfseries fire\+\_\+1\+\_\+altitude} = 0
\item 
\Hypertarget{main_8cpp_a60d58f870e209d51c61f0890aa06fb70}\label{main_8cpp_a60d58f870e209d51c61f0890aa06fb70} 
uint8\+\_\+t {\bfseries fire\+\_\+2\+\_\+altitude} = 0
\item 
\Hypertarget{main_8cpp_a8b532886584712aa1f5cb5d08452d682}\label{main_8cpp_a8b532886584712aa1f5cb5d08452d682} 
uint8\+\_\+t {\bfseries fire\+\_\+3\+\_\+altitude} = 0
\item 
\Hypertarget{main_8cpp_ab1f3a0b6aa534a54086b55307599c9fa}\label{main_8cpp_ab1f3a0b6aa534a54086b55307599c9fa} 
uint8\+\_\+t {\bfseries fire\+\_\+4\+\_\+altitude} = 0
\end{DoxyCompactItemize}

\doxysubsection{Detailed Description}
Main file for the Ardentis flight computer code. 

\begin{DoxyAuthor}{Author}
Roland Neill 
\end{DoxyAuthor}
\begin{DoxyVersion}{Version}
0.\+1-\/alpha 
\end{DoxyVersion}
\begin{DoxyDate}{Date}
2025-\/04-\/25
\end{DoxyDate}
\begin{DoxyCopyright}{Copyright}
Copyright (c) 2025 
\end{DoxyCopyright}

\doxysubsection{Function Documentation}
\Hypertarget{main_8cpp_afe461d27b9c48d5921c00d521181f12f}\index{main.cpp@{main.cpp}!loop@{loop}}
\index{loop@{loop}!main.cpp@{main.cpp}}
\doxysubsubsection{\texorpdfstring{loop()}{loop()}}
{\footnotesize\ttfamily \label{main_8cpp_afe461d27b9c48d5921c00d521181f12f} 
void loop (\begin{DoxyParamCaption}{}{}\end{DoxyParamCaption})}

\begin{DoxyCode}{0}
\DoxyCodeLine{00160\ \ \ \ \ \ \ \ \ \ \ \ \ \{}
\DoxyCodeLine{00161\ }
\DoxyCodeLine{00162\ \ \ \ \ \mbox{\hyperlink{struct_ard_data_struct}{ArdDataStruct}}\ data;}
\DoxyCodeLine{00163\ \ \ }
\DoxyCodeLine{00164\ \ \ \ \ sensors.update();}
\DoxyCodeLine{00165\ }
\DoxyCodeLine{00166\ }
\DoxyCodeLine{00167\ }
\DoxyCodeLine{00168\ \ \ \ \ \textcolor{comment}{//\ Check\ Continuity}}
\DoxyCodeLine{00169\ \ \ \ \ data.cont1\ =\ digitalRead(ARD\_CONT1);}
\DoxyCodeLine{00170\ \ \ \ \ data.cont2\ =\ digitalRead(ARD\_CONT2);}
\DoxyCodeLine{00171\ \ \ \ \ data.cont3\ =\ digitalRead(ARD\_CONT3);}
\DoxyCodeLine{00172\ \ \ \ \ data.cont4\ =\ digitalRead(ARD\_CONT4);}
\DoxyCodeLine{00173\ }
\DoxyCodeLine{00174\ }
\DoxyCodeLine{00175\ \ \ \ \ \textcolor{keywordflow}{for}\ (\textcolor{keywordtype}{int}\ i\ =\ 1;\ i\ <=\ 4;\ i++)\ \{}
\DoxyCodeLine{00176\ \ \ \ \ \ \ \ \ uint8\_t\ fire\_mode\ =\ 0;}
\DoxyCodeLine{00177\ \ \ \ \ \ \ \ \ uint16\_t\ fire\_param\ =\ 0;}
\DoxyCodeLine{00178\ \ \ \ \ \ \ \ \ \textcolor{keywordtype}{bool}*\ fire\_signal\ =\ \textcolor{keyword}{nullptr};}
\DoxyCodeLine{00179\ \ \ \ \ \ \ \ \ \textcolor{keywordtype}{bool}*\ data\_signal\ =\ \textcolor{keyword}{nullptr};}
\DoxyCodeLine{00180\ }
\DoxyCodeLine{00181\ \ \ \ \ \ \ \ \ \textcolor{keywordflow}{switch}\ (i)\ \{}
\DoxyCodeLine{00182\ \ \ \ \ \ \ \ \ \textcolor{keywordflow}{case}\ 1:}
\DoxyCodeLine{00183\ \ \ \ \ \ \ \ \ \ \ \ \ fire\_mode\ =\ fire\_1\_mode;}
\DoxyCodeLine{00184\ \ \ \ \ \ \ \ \ \ \ \ \ fire\_param\ =\ fire\_1\_param;}
\DoxyCodeLine{00185\ \ \ \ \ \ \ \ \ \ \ \ \ fire\_signal\ =\ \&fire\_signal\_1;}
\DoxyCodeLine{00186\ \ \ \ \ \ \ \ \ \ \ \ \ data\_signal\ =\ \&data.fired\_1;}
\DoxyCodeLine{00187\ \ \ \ \ \ \ \ \ \ \ \ \ \textcolor{keywordflow}{break};}
\DoxyCodeLine{00188\ \ \ \ \ \ \ \ \ \textcolor{keywordflow}{case}\ 2:}
\DoxyCodeLine{00189\ \ \ \ \ \ \ \ \ \ \ \ \ fire\_mode\ =\ fire\_2\_mode;}
\DoxyCodeLine{00190\ \ \ \ \ \ \ \ \ \ \ \ \ fire\_param\ =\ fire\_2\_param;}
\DoxyCodeLine{00191\ \ \ \ \ \ \ \ \ \ \ \ \ fire\_signal\ =\ \&fire\_signal\_2;}
\DoxyCodeLine{00192\ \ \ \ \ \ \ \ \ \ \ \ \ data\_signal\ =\ \&data.fired\_2;}
\DoxyCodeLine{00193\ \ \ \ \ \ \ \ \ \ \ \ \ \textcolor{keywordflow}{break};}
\DoxyCodeLine{00194\ \ \ \ \ \ \ \ \ \textcolor{keywordflow}{case}\ 3:}
\DoxyCodeLine{00195\ \ \ \ \ \ \ \ \ \ \ \ \ fire\_mode\ =\ fire\_3\_mode;}
\DoxyCodeLine{00196\ \ \ \ \ \ \ \ \ \ \ \ \ fire\_param\ =\ fire\_3\_param;}
\DoxyCodeLine{00197\ \ \ \ \ \ \ \ \ \ \ \ \ fire\_signal\ =\ \&fire\_signal\_3;}
\DoxyCodeLine{00198\ \ \ \ \ \ \ \ \ \ \ \ \ data\_signal\ =\ \&data.fired\_3;}
\DoxyCodeLine{00199\ \ \ \ \ \ \ \ \ \ \ \ \ \textcolor{keywordflow}{break};}
\DoxyCodeLine{00200\ \ \ \ \ \ \ \ \ \textcolor{keywordflow}{case}\ 4:}
\DoxyCodeLine{00201\ \ \ \ \ \ \ \ \ \ \ \ \ fire\_mode\ =\ fire\_4\_mode;}
\DoxyCodeLine{00202\ \ \ \ \ \ \ \ \ \ \ \ \ fire\_param\ =\ fire\_4\_param;}
\DoxyCodeLine{00203\ \ \ \ \ \ \ \ \ \ \ \ \ fire\_signal\ =\ \&fire\_signal\_4;}
\DoxyCodeLine{00204\ \ \ \ \ \ \ \ \ \ \ \ \ data\_signal\ =\ \&data.fired\_4;}
\DoxyCodeLine{00205\ \ \ \ \ \ \ \ \ \ \ \ \ \textcolor{keywordflow}{break};}
\DoxyCodeLine{00206\ \ \ \ \ \ \ \ \ \}}
\DoxyCodeLine{00207\ \ \ \ \ \ \ \ \ \textcolor{comment}{//\ Check\ if\ the\ fire\ mode\ is\ active}}
\DoxyCodeLine{00208\ \ \ \ \ \ \ \ \ \textcolor{keywordflow}{if}\ (fire\_mode\ ==\ 1)\ \{\ \textcolor{comment}{//\ Fire\ at\ apogee}}
\DoxyCodeLine{00209\ \ \ \ \ \ \ \ \ \ \ \ \ \textcolor{keywordflow}{if}\ (apogee\ ==\ \textcolor{keyword}{true}\ \&\&\ time\_since\_apogee\ >\ fire\_param)\ \{}
\DoxyCodeLine{00210\ \ \ \ \ \ \ \ \ \ \ \ \ \ \ \ \ *fire\_signal\ =\ \textcolor{keyword}{true};}
\DoxyCodeLine{00211\ \ \ \ \ \ \ \ \ \ \ \ \ \ \ \ \ *data\_signal\ =\ \textcolor{keyword}{true};}
\DoxyCodeLine{00212\ \ \ \ \ \ \ \ \ \ \ \ \ \}\ \textcolor{keywordflow}{else}\ \{}
\DoxyCodeLine{00213\ \ \ \ \ \ \ \ \ \ \ \ \ \ \ \ \ *fire\_signal\ =\ \textcolor{keyword}{false};}
\DoxyCodeLine{00214\ \ \ \ \ \ \ \ \ \ \ \ \ \}}
\DoxyCodeLine{00215\ \ \ \ \ \ \ \ \ \}\ \textcolor{keywordflow}{else}\ \textcolor{keywordflow}{if}\ (fire\_mode\ ==\ 2)\ \{\ \textcolor{comment}{//\ Fire\ at\ or\ below\ set\ altitude\ on\ descent}}
\DoxyCodeLine{00216\ \ \ \ \ \ \ \ \ \ \ \ \ *fire\_signal\ =\ (altitude\ <=\ fire\_param)\ \&\&\ (descending\ ==\ \textcolor{keyword}{true});}
\DoxyCodeLine{00217\ \ \ \ \ \ \ \ \ \}\ \textcolor{keywordflow}{else}\ \textcolor{keywordflow}{if}\ (fire\_mode\ ==\ 3)\ \{\ \textcolor{comment}{//\ Fire\ at\ or\ above\ set\ altitude\ on\ ascent}}
\DoxyCodeLine{00218\ \ \ \ \ \ \ \ \ \ \ \ \ *fire\_signal\ =\ (altitude\ >=\ fire\_param)\ \&\&\ (ascending\ ==\ \textcolor{keyword}{true});}
\DoxyCodeLine{00219\ \ \ \ \ \ \ \ \ \}\ \textcolor{keywordflow}{else}\ \textcolor{keywordflow}{if}\ (fire\_mode\ ==\ 4)\ \{\ \textcolor{comment}{//\ Fire\ at\ set\ time\ after\ liftoff}}
\DoxyCodeLine{00220\ \ \ \ \ \ \ \ \ \ \ \ \ *fire\_signal\ =\ time\_since\_apogee\ >\ fire\_param;}
\DoxyCodeLine{00221\ \ \ \ \ \ \ \ \ \}\ \textcolor{keywordflow}{else}\ \{}
\DoxyCodeLine{00222\ \ \ \ \ \ \ \ \ \ \ \ \ *fire\_signal\ =\ \textcolor{keyword}{false};}
\DoxyCodeLine{00223\ \ \ \ \ \ \ \ \ \}}
\DoxyCodeLine{00224\ \ \ \ \ \}}
\DoxyCodeLine{00225\ }
\DoxyCodeLine{00226\ \ \ \ \ \textcolor{keywordflow}{if}\ (!radio.busy)\ \{}
\DoxyCodeLine{00227\ \ \ \ \ \ \ \ \ \mbox{\hyperlink{struct_radio_packet}{RadioPacket}}\ radioPacket;}
\DoxyCodeLine{00228\ \ \ \ \ \ \ \ \ strncpy(radioPacket.callsign,\ \textcolor{stringliteral}{"{}VE3FSZ"{}},\ \textcolor{keyword}{sizeof}(radioPacket.callsign)\ -\/\ 1);}
\DoxyCodeLine{00229\ \ \ \ \ \ \ \ \ radioPacket.callsign[\textcolor{keyword}{sizeof}(radioPacket.callsign)\ -\/\ 1]\ =\ \textcolor{charliteral}{'\(\backslash\)0'};}
\DoxyCodeLine{00230\ \ \ \ \ \ \ \ \ radioPacket.latitude\ =\ data.latitude;}
\DoxyCodeLine{00231\ \ \ \ \ \ \ \ \ radioPacket.longitude\ =\ data.longitude;}
\DoxyCodeLine{00232\ \ \ \ \ \ \ \ \ radioPacket.altitude\ =\ data.altitude;}
\DoxyCodeLine{00233\ }
\DoxyCodeLine{00234\ \ \ \ \ \ \ \ \ radio.sendData(radioPacket);}
\DoxyCodeLine{00235\ }
\DoxyCodeLine{00236\ }
\DoxyCodeLine{00237\ \ \ \ \ \ \ \ \ Serial.println(F(\textcolor{stringliteral}{"{}[RADIO]\ Sending\ packet"{}}));}
\DoxyCodeLine{00238\ }
\DoxyCodeLine{00239\ \ \ \ \ \ \ \ \ \textcolor{keywordflow}{if}\ (fire\_signal\_1)\ \{}
\DoxyCodeLine{00240\ \ \ \ \ \ \ \ \ \ \ \ \ Serial.println(\textcolor{stringliteral}{"{}[OUTPUT]\ Firing\ Output\ 1."{}});}
\DoxyCodeLine{00241\ \ \ \ \ \ \ \ \ \ \ \ \ digitalWrite(ARD\_FIRE1,\ LOW);}
\DoxyCodeLine{00242\ \ \ \ \ \ \ \ \ \ \ \ \ delay(1000);}
\DoxyCodeLine{00243\ \ \ \ \ \ \ \ \ \ \ \ \ digitalWrite(ARD\_FIRE1,\ HIGH);}
\DoxyCodeLine{00244\ \ \ \ \ \ \ \ \ \}}
\DoxyCodeLine{00245\ \ \ \ \ \}}
\DoxyCodeLine{00246\ \}}

\end{DoxyCode}
\Hypertarget{main_8cpp_a7dfd9b79bc5a37d7df40207afbc5431f}\index{main.cpp@{main.cpp}!setup@{setup}}
\index{setup@{setup}!main.cpp@{main.cpp}}
\doxysubsubsection{\texorpdfstring{setup()}{setup()}}
{\footnotesize\ttfamily \label{main_8cpp_a7dfd9b79bc5a37d7df40207afbc5431f} 
void setup (\begin{DoxyParamCaption}\item[{void}]{}{}\end{DoxyParamCaption})}

\begin{DoxyCode}{0}
\DoxyCodeLine{00107\ \ \ \ \ \ \ \ \ \ \ \ \ \ \ \ \ \ \{}
\DoxyCodeLine{00108\ \ \ \ \ Serial.begin(115200);}
\DoxyCodeLine{00109\ \ \ \ \ \textcolor{keywordflow}{while}\ (!Serial)\ delay(10);}
\DoxyCodeLine{00110\ }
\DoxyCodeLine{00111\ \ \ \ \ radio.begin(radioConfig);}
\DoxyCodeLine{00112\ \ \ \ \ radio.setTxInt(txCallback);}
\DoxyCodeLine{00113\ }
\DoxyCodeLine{00114\ \ \ \ \ \textcolor{keywordflow}{if}\ (sensors.initSensors(0x18,\ 0x68,\ 0x77,\ ARD\_GPS\_BAUD)\ !=\ ERROR\_NONE)\ \{}
\DoxyCodeLine{00115\ \ \ \ \ \ \ \ \ main\_log.error(\textcolor{stringliteral}{"{}Sensor\ initialization\ failed."{}});}
\DoxyCodeLine{00116\ \ \ \ \ \}\ \textcolor{keywordflow}{else}\ \{}
\DoxyCodeLine{00117\ \ \ \ \ \ \ \ \ main\_log.info(\textcolor{stringliteral}{"{}Sensor\ initialization\ successful."{}});}
\DoxyCodeLine{00118\ \ \ \ \ \}}
\DoxyCodeLine{00119\ }
\DoxyCodeLine{00120\ }
\DoxyCodeLine{00121\ \ \ \ \ \textcolor{comment}{//\ SD\ Card\ Setup}}
\DoxyCodeLine{00122\ \ \ \ \ \textcolor{keywordflow}{if}\ (!SD.begin(4))\ \{}
\DoxyCodeLine{00123\ \ \ \ \ \ \ \ \ Serial.println(\textcolor{stringliteral}{"{}[ERROR]\ SD\ initialization\ failed!"{}});}
\DoxyCodeLine{00124\ \ \ \ \ \ \ \ \ \textcolor{keywordflow}{while}\ (1);}
\DoxyCodeLine{00125\ \ \ \ \ \}}
\DoxyCodeLine{00126\ \ \ \ \ Serial.println(\textcolor{stringliteral}{"{}[SD]\ initialization\ done."{}});}
\DoxyCodeLine{00127\ }
\DoxyCodeLine{00128\ \ \ \ \ flightLog\ =\ SD.open(\textcolor{stringliteral}{"{}flight.log"{}},\ FILE\_WRITE);}
\DoxyCodeLine{00129\ \ \ \ \ \textcolor{keywordflow}{if}\ (flightLog)\ \{}
\DoxyCodeLine{00130\ \ \ \ \ \ \ \ \ Serial.print(\textcolor{stringliteral}{"{}[SD]\ Writing\ to\ flight.log..."{}});}
\DoxyCodeLine{00131\ \ \ \ \ \ \ \ \ flightLog.println(\textcolor{stringliteral}{"{}testing\ 1,\ 2,\ 3."{}});}
\DoxyCodeLine{00132\ \ \ \ \ \ \ \ \ \textcolor{comment}{//\ close\ the\ file:}}
\DoxyCodeLine{00133\ \ \ \ \ \ \ \ \ flightLog.close();}
\DoxyCodeLine{00134\ \ \ \ \ \ \ \ \ Serial.println(\textcolor{stringliteral}{"{}[SD]\ Done\ writing\ to\ flight.log"{}});}
\DoxyCodeLine{00135\ \ \ \ \ \}\ \textcolor{keywordflow}{else}\ \{}
\DoxyCodeLine{00136\ \ \ \ \ \ \ \ \ \textcolor{comment}{//\ if\ the\ file\ didn't\ open,\ print\ an\ error:}}
\DoxyCodeLine{00137\ \ \ \ \ \ \ \ \ Serial.println(\textcolor{stringliteral}{"{}[ERROR]\ Error\ opening\ flight.log"{}});}
\DoxyCodeLine{00138\ }
\DoxyCodeLine{00139\ \ \ \ \ \}}
\DoxyCodeLine{00140\ }
\DoxyCodeLine{00141\ \ \ \ \ \textcolor{comment}{//\ Initialize\ Fire\ Output\ GPIOs}}
\DoxyCodeLine{00142\ \ \ \ \ pinMode(ARD\_FIRE1,\ OUTPUT);}
\DoxyCodeLine{00143\ \ \ \ \ digitalWrite(ARD\_FIRE1,\ HIGH);}
\DoxyCodeLine{00144\ \ \ \ \ pinMode(ARD\_FIRE2,\ OUTPUT);}
\DoxyCodeLine{00145\ \ \ \ \ digitalWrite(ARD\_FIRE2,\ HIGH);}
\DoxyCodeLine{00146\ \ \ \ \ pinMode(ARD\_FIRE3,\ OUTPUT);}
\DoxyCodeLine{00147\ \ \ \ \ digitalWrite(ARD\_FIRE3,\ HIGH);}
\DoxyCodeLine{00148\ \ \ \ \ pinMode(ARD\_FIRE4,\ OUTPUT);}
\DoxyCodeLine{00149\ \ \ \ \ digitalWrite(ARD\_FIRE4,\ HIGH);}
\DoxyCodeLine{00150\ }
\DoxyCodeLine{00151\ \ \ \ \ pinMode(ARD\_CONT1,\ INPUT\_PULLUP);}
\DoxyCodeLine{00152\ \ \ \ \ pinMode(ARD\_CONT2,\ INPUT\_PULLUP);}
\DoxyCodeLine{00153\ \ \ \ \ pinMode(ARD\_CONT3,\ INPUT\_PULLUP);}
\DoxyCodeLine{00154\ \ \ \ \ pinMode(ARD\_CONT4,\ INPUT\_PULLUP);}
\DoxyCodeLine{00155\ }
\DoxyCodeLine{00156\ \ \ \ \ Serial.println(\textcolor{stringliteral}{"{}[OUTPUT]\ Output\ GPIOs\ initialized."{}});}
\DoxyCodeLine{00157\ }
\DoxyCodeLine{00158\ \ \ \ \ \}}

\end{DoxyCode}
\Hypertarget{main_8cpp_a94b7c389e4d61e6c9d8d34356c7919e8}\index{main.cpp@{main.cpp}!txCallback@{txCallback}}
\index{txCallback@{txCallback}!main.cpp@{main.cpp}}
\doxysubsubsection{\texorpdfstring{txCallback()}{txCallback()}}
{\footnotesize\ttfamily \label{main_8cpp_a94b7c389e4d61e6c9d8d34356c7919e8} 
void tx\+Callback (\begin{DoxyParamCaption}\item[{void}]{}{}\end{DoxyParamCaption})}

\begin{DoxyCode}{0}
\DoxyCodeLine{00050\ \ \ \ \ \ \ \ \ \ \ \ \ \ \ \ \ \ \ \ \ \ \ \{}
\DoxyCodeLine{00051\ \ \ \ \ \textcolor{comment}{//\ Callback\ function\ for\ when\ the\ radio\ is\ done\ transmitting}}
\DoxyCodeLine{00052\ \ \ \ \ radio.doneTX();}
\DoxyCodeLine{00053\ \}}

\end{DoxyCode}

\doxysubsection{Variable Documentation}
\Hypertarget{main_8cpp_ae75c26b3f0347f4abceb163265d2faf4}\index{main.cpp@{main.cpp}!radioConfig@{radioConfig}}
\index{radioConfig@{radioConfig}!main.cpp@{main.cpp}}
\doxysubsubsection{\texorpdfstring{radioConfig}{radioConfig}}
{\footnotesize\ttfamily \label{main_8cpp_ae75c26b3f0347f4abceb163265d2faf4} 
\mbox{\hyperlink{structard___radio_config__t}{ard\+\_\+\+Radio\+Config\+\_\+t}} radio\+Config}

{\bfseries Initial value\+:}
\begin{DoxyCode}{0}
\DoxyCodeLine{=\ \{}
\DoxyCodeLine{\ \ \ \ ARD\_RADIO\_FREQ,}
\DoxyCodeLine{\ \ \ \ ARD\_LORA\_BW,}
\DoxyCodeLine{\ \ \ \ ARD\_LORA\_SF,}
\DoxyCodeLine{\ \ \ \ ARD\_LORA\_CR,}
\DoxyCodeLine{\ \ \ \ ARD\_LORA\_SYNCWORD,}
\DoxyCodeLine{\ \ \ \ ARD\_RADIO\_TX\_PWR}
\DoxyCodeLine{\}}

\end{DoxyCode}

\begin{DoxyCode}{0}
\DoxyCodeLine{00019\ \ \ \ \ \ \ \ \ \ \ \ \ \ \ \ \ \ \ \ \ \ \ \ \ \ \ \ \ \ \ \ \ \{}
\DoxyCodeLine{00020\ \ \ \ \ ARD\_RADIO\_FREQ,}
\DoxyCodeLine{00021\ \ \ \ \ ARD\_LORA\_BW,}
\DoxyCodeLine{00022\ \ \ \ \ ARD\_LORA\_SF,}
\DoxyCodeLine{00023\ \ \ \ \ ARD\_LORA\_CR,}
\DoxyCodeLine{00024\ \ \ \ \ ARD\_LORA\_SYNCWORD,}
\DoxyCodeLine{00025\ \ \ \ \ ARD\_RADIO\_TX\_PWR}
\DoxyCodeLine{00026\ \};}

\end{DoxyCode}
\Hypertarget{main_8cpp_a52c567d1d8398c2a5f2574ccd2ab895a}\index{main.cpp@{main.cpp}!radioPins@{radioPins}}
\index{radioPins@{radioPins}!main.cpp@{main.cpp}}
\doxysubsubsection{\texorpdfstring{radioPins}{radioPins}}
{\footnotesize\ttfamily \label{main_8cpp_a52c567d1d8398c2a5f2574ccd2ab895a} 
\mbox{\hyperlink{structard___radio_pins__t}{ard\+\_\+\+Radio\+Pins\+\_\+t}} radio\+Pins}

{\bfseries Initial value\+:}
\begin{DoxyCode}{0}
\DoxyCodeLine{=\ \{}
\DoxyCodeLine{\ \ \ \ ARD\_RADIO\_NSS,}
\DoxyCodeLine{\ \ \ \ ARD\_RADIO\_BUSY,}
\DoxyCodeLine{\ \ \ \ ARD\_RADIO\_NRST,}
\DoxyCodeLine{\ \ \ \ ARD\_RADIO\_DIO1,}
\DoxyCodeLine{\ \ \ \ ARD\_RADIO\_SPI\_MISO,}
\DoxyCodeLine{\ \ \ \ ARD\_RADIO\_SPI\_MOSI,}
\DoxyCodeLine{\ \ \ \ ARD\_RADIO\_SPI\_SCK}
\DoxyCodeLine{\}}

\end{DoxyCode}

\begin{DoxyCode}{0}
\DoxyCodeLine{00027\ \ \ \ \ \ \ \ \ \ \ \ \ \ \ \ \ \ \ \ \ \ \ \ \ \ \ \ \ \{}
\DoxyCodeLine{00028\ \ \ \ \ ARD\_RADIO\_NSS,}
\DoxyCodeLine{00029\ \ \ \ \ ARD\_RADIO\_BUSY,}
\DoxyCodeLine{00030\ \ \ \ \ ARD\_RADIO\_NRST,}
\DoxyCodeLine{00031\ \ \ \ \ ARD\_RADIO\_DIO1,}
\DoxyCodeLine{00032\ \ \ \ \ ARD\_RADIO\_SPI\_MISO,}
\DoxyCodeLine{00033\ \ \ \ \ ARD\_RADIO\_SPI\_MOSI,}
\DoxyCodeLine{00034\ \ \ \ \ ARD\_RADIO\_SPI\_SCK}
\DoxyCodeLine{00035\ \};}

\end{DoxyCode}

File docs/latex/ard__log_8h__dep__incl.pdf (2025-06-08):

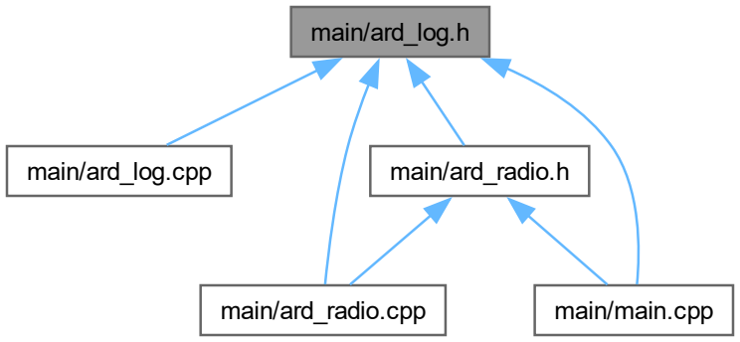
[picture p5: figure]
main/ard_log.h; main/ard_log.cpp; main/ard_radio.cpp; main/ard_radio.h; main/main.cpp

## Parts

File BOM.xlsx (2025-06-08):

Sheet: Rocket
Item | Use | Link | QTY Needed | Units | Price per unit | Line Cost | Option A | Option B | Option C | Option D | McMaster-Carr | Option A: | $135.65
Rail Guides |  | https://www.allrockets.ca/Build/Rail/Delrin-Rail-Gudes/1010-Airframe | 1 | 2/EA | $4.90 | $4.90 | TRUE | TRUE | TRUE | FALSE |  | Option B: | $62.36
Swivel |  | https://www.allrockets.ca/Build/Swivels-Links/Swivel-6 | 2 | EA | $2.80 | $5.60 | TRUE | TRUE | TRUE | FALSE |  | Option C | $109.05
Quick Link |  | https://www.allrockets.ca/Build/Swivels-Links/Swivel-6 | 0 | EA | $2.70 | $0.00 | TRUE | TRUE | TRUE | FALSE |  | Option D: | $0.00
Phenolic Tube |  | https://www.allrockets.ca/Build/Airframes/Phenolic/40 | 1 | 36" | $39.20 | $39.20 | TRUE | FALSE | TRUE | FALSE
Cardboard Tube |  | https://www.allrockets.ca/Build/Airframes/40 | 1 | 36" | $19.60 | $19.60 | FALSE | TRUE | FALSE | FALSE
Phenolic Coupler | Can be bought in bulk | https://www.allrockets.ca/Build/Couplers/Phenolic/4.0 | 1 | 7" | $11.00 | $11.00 | TRUE | FALSE | TRUE | FALSE
Cardboard Coupler |  | https://www.allrockets.ca/Build/Couplers/40 | 1 | 8" | $9.80 | $9.80 | FALSE | TRUE | FALSE | FALSE
54mm Motor Tube |  | https://www.allrockets.ca/Build/Motor-Tubes/54 | 1 | 24" | $9.00 | $9.00 | FALSE | FALSE | FALSE | FALSE
38mm Motor Tube |  | https://www.allrockets.ca/Build/Motor-Tubes/38 | 1 | 24" | $6.20 | $6.20 | FALSE | TRUE | FALSE | FALSE
54mm Phenolic Motor Tube |  | https://www.allrockets.ca/Build/Motor-Tubes/P/54 | 1 | 17.75" | $15.60 | $15.60 | TRUE | FALSE | FALSE | FALSE
38mm Penolic Motor Tube |  | https://www.allrockets.ca/Build/Motor-Tubes/P/38 | 1 | 17.75" | $14.00 | $14.00 | TRUE | FALSE | TRUE | FALSE
Parachute |  |  |  |  |  | $0.00 | FALSE | FALSE | FALSE | FALSE
#8 Hex Nut | Nosecone and motor retention | https://catalogue.ottawafastenersupply.com/product/hex-nut-8-stainless-steel-coarse-thread-mml038 | 12 | EA | $0.05 | $0.60 | TRUE | TRUE | TRUE | FALSE | 90480A009
#8-32 X 1.5" Bolt | Motor Retention Bolts | https://catalogue.ottawafastenersupply.com/product/fasteners-and-fittings-inc-pan-head-machine-screws-117506-mmq603 | 3 | EA | $0.06 | $0.18 | TRUE | TRUE | TRUE | FALSE | 90272A203
#8-32 X 0.5" Bolt | Nosecone Retention Bolts | https://catalogue.ottawafastenersupply.com/product/fasteners-and-fittings-inc-pan-head-machine-screws-117407-mmq598 | 6 | EA | $0.06 | $0.36 | TRUE | TRUE | TRUE | FALSE | 90272A194
#10-24 T-nut | Put threads in wood | https://www.homedepot.ca/product/paulin-10-24-tee-nuts-4-prong-5-16-inch-barrel-length/1000129425 | 3 | EA | $0.41 | $1.23 | TRUE | TRUE | TRUE | FALSE | 90975A301
#10-24 X 0.75" Bolt | Attach Upper motor retainer | https://catalogue.ottawafastenersupply.com/product/fasteners-and-fittings-inc-pan-head-machine-screws-117582-mmq616 | 3 | EA | $0.05 | $0.15 | TRUE | TRUE | TRUE | FALSE | 90272A245
1/4-20 Eye Bolt | Attach Recovery harness to rocket | https://www.allrockets.ca/Build/Swivels-Links/Eye-Bolt-14 | 3 | EA | $4.20 | $12.60 | TRUE | TRUE | TRUE | FALSE | 3032T41
1/4-20 Nut | Eyebolt Nut | https://catalogue.ottawafastenersupply.com/product/hex-nut-1-4-zinc-cr-3-coarse-thread-mmm965 | 6 | EA | $0.03 | $0.18 | TRUE | TRUE | TRUE | FALSE | 95462A029
1/4" Fender Washer | Eyebolt Fender Washer | https://www.homedepot.ca/product/paulin-1-4-inch-bolt-size-flat-washers-hot-dipped-galvanized-1pc/1000141551 | 6 | EA | $0.16 | $0.96 | TRUE | TRUE | TRUE | FALSE | 91860A029
1/4" Lock Washer | Eyebolt and #10 Bolt Lock Washer | https://catalogue.ottawafastenersupply.com/product/split-lock-washer-1-4-yellow-zinc-ge232 | 9 | EA | $0.02 | $0.18 | TRUE | TRUE | TRUE | FALSE | 91104A029
1/4" Washer | Eyebolt Washer | https://catalogue.ottawafastenersupply.com/product/sae-flat-washer-1-4-yellow-zinc-ge242 | 6 | EA | $0.11 | $0.66 | TRUE | TRUE | TRUE | FALSE | 98023A029
#8 Washers | Washer for #8 bolts | https://www.homedepot.ca/product/paulin--8-sae-flat-washers-zinc-plated-18-pcs-/1001588236 | 1 | 18/EA | $3.97 | $3.97 | TRUE | TRUE | TRUE | FALSE | 90126A512
5mm Lock Washer | Lock Washer for #8 Bolts | https://catalogue.ottawafastenersupply.com/product/split-lock-washer-5-mm-stainless-steel-mmm592 | 1 | EA | $0.03 | $0.03 | TRUE | TRUE | TRUE | FALSE | 92148A170
#10 Washer | Washer for #10 Bolts | https://www.homedepot.ca/product/paulin--10-steel-s-a-e-washers-zinc-plated/1000128785 | 3 | EA | $0.15 | $0.45 | TRUE | TRUE | TRUE | FALSE | 90126A514
Nomex Blanket | Prevent rocket from becoming literal dumpster fire | https://www.allrockets.ca/Accessories/Chute-Protector-12 | 1 | EA | $12.80 | $12.80 | TRUE | TRUE | TRUE | FALSE
EggTimer Quantum | Get max altitude of rocket |  | 1 | EA | $40 | $40.00 | FALSE | FALSE | FALSE | FALSE
Shock Cord |  | https://www.allrockets.ca/Build/Shock-Cords/Tubular/15 | 5 | 1m | $2.20 | $11.00 | TRUE | TRUE | FALSE | FALSE
 |  |  |  |  |  |  | FALSE | FALSE | FALSE | FALSE
 |  |  |  |  |  |  | FALSE | FALSE | FALSE | FALSE
 |  |  |  |  |  |  | FALSE | FALSE | FALSE | FALSE
 |  |  |  |  |  |  | FALSE | FALSE | FALSE | FALSE
 |  |  |  |  |  |  | FALSE | FALSE | FALSE | FALSE
 |  |  |  |  |  |  | FALSE | FALSE | FALSE | FALSE
 |  |  |  |  |  |  | FALSE | FALSE | FALSE | FALSE
 |  |  |  |  |  |  | FALSE | FALSE | FALSE | FALSE
 |  |  |  |  |  |  | FALSE | FALSE | FALSE | FALSE
 |  |  |  |  |  |  | FALSE | FALSE | FALSE | FALSE
 |  |  |  |  |  |  | FALSE | FALSE | FALSE | FALSE
 |  |  |  |  |  |  | FALSE | FALSE | FALSE | FALSE
 |  |  |  |  |  |  | FALSE | FALSE | FALSE | FALSE
 |  |  |  |  |  |  | FALSE | FALSE | FALSE | FALSE
 |  |  |  |  |  |  | FALSE | FALSE | FALSE | FALSE
 |  |  |  |  |  |  | FALSE | FALSE | FALSE | FALSE
 |  |  |  |  |  |  | FALSE | FALSE | FALSE | FALSE
 |  |  |  |  |  |  | FALSE | FALSE | FALSE | FALSE
 |  |  |  |  |  |  | FALSE | FALSE | FALSE | FALSE
 |  |  |  |  |  |  | FALSE | FALSE | FALSE | FALSE
 |  |  |  |  |  |  | FALSE | FALSE | FALSE | FALSE

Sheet: Avionics
Flight
Part | Qty | Designator | Supplier | DigiKey Part Number | Mouser Part Number | DigiKey Cost | Mouser Cost | Line Cost | Has Library? | Column1 | Ardentis Basic |  |  |  |  | Number of people Buying
USB Connector | 2 | J6 | Digikey | 2223-UJ2-MIBH-G-SMT-TR-ND | 490-UJ2-MIBH-G-SMTTR | $0.67 | $0.58 | $1.34 | Yes |  | Parts Total | JLC Ship | DigiKey Ship | Mouser Ship | Per Person w Tax | 1
Inductor | 2 | L1 | Digikey | 3526-WIP252012S-2R2MLDGTR-ND |  | $0.15 |  | $0.30 | Yes |  | $173.69 | $3.00 | $0.00 | $0.00 | $199.66
0 Ohm Resistor | 4 | R11,R13 | Digikey | P0.0ATR-ND | 594-RCA08050000ZSEC | $0.16 | $0.17 | $0.64 | Yes |  |  |  |  |  |  | Mouser | Digikey
Radio Module | 2 | U1 | Digikey | 1597-114993390-ND |  | $7.83 |  | $15.66 |  |  |  |  |  |  |  | 0 | 148.688
Buck Converter | 2 | U7 | Digikey | RT6150B-33GQWTR-ND | 835-RT6150B-33GQW | $4.62 | $4.53 | $9.24
MCU | 2 | U8 | Digikey | 1965-ESP32-S3-MINI-1-N4R2TR-ND |  | $8.40 |  | $16.80
22uF Cap | 10 | C1,C4,C7,C11,C12,C13,C17 | Digikey | 1276-3031-2-ND |  | $0.20 |  | $2.00
0.1 uF Cap | 12 | C2,C3,C5,C6,C8,C9,C10,C14,C15,C16 | Digikey | 478-KGM21NR71H104KTTR-ND |  | $0.12 |  | $1.44
Terminal Blocks | 4 | J2,J3,J4 | Digikey | 102-6136-ND |  | $0.85 |  | $3.40
10k Resistors | 22 | R1,R2,R3,R4,R5,R6,R7,R8,R9,R10,R12,R14,R15,R16,R17,R18,R19 | Digikey | 311-10KARTR-ND |  | $0.02 |  | $0.42
Diodes | 4 | D1,D2,D3,D4 | Digikey | BAT42WRHGTR-ND |  | $0.17 |  | $0.68
SD Card Slot | 1 | J5 | Digikey | 2073-MEM2067-02-180-00-ATR-ND |  | $1.60 |  | $1.60
Deployment Transistors | 2 | Q1,Q2 | Digikey | 3141-G170P02D32TR-ND |  | $1.01 |  | $2.02
GPS | 1 | U2 | Digikey |  |  | $50.76 | $48.04 | $50.76
Accelerometer | 1 | U3 | Digikey | 1428-ICM-42670-PTR-ND |  | $5.90 |  | $5.90
High G Accelerometer | 1 | U4 | Digikey | 497-13903-2-ND | 511-H3LIS331DLTR | $17.79 | $16.84 | $17.79
Magnetometer | 1 | U5 | Digikey | 497-17588-2-ND | 511-LIS2MDLTR | $3.71 | $3.51 | $3.71 |  | Consider deleting. Appears to be very hard to work with.
Barometer | 1 | U6 | Digikey | 223-1622-2-ND |  | $14.99 |  | $14.99
SD Card | 1 |  |  |  |  | $10.00 |  | $10.00
Antennas | 2 |  |  |  |  | $5.00 |  | $10.00
PCB | 1 |  |  |  |  | $5.00 |  | $5.00
GPS Antenna | 0 |  |  |  |  | $7.50 |  | $0.00

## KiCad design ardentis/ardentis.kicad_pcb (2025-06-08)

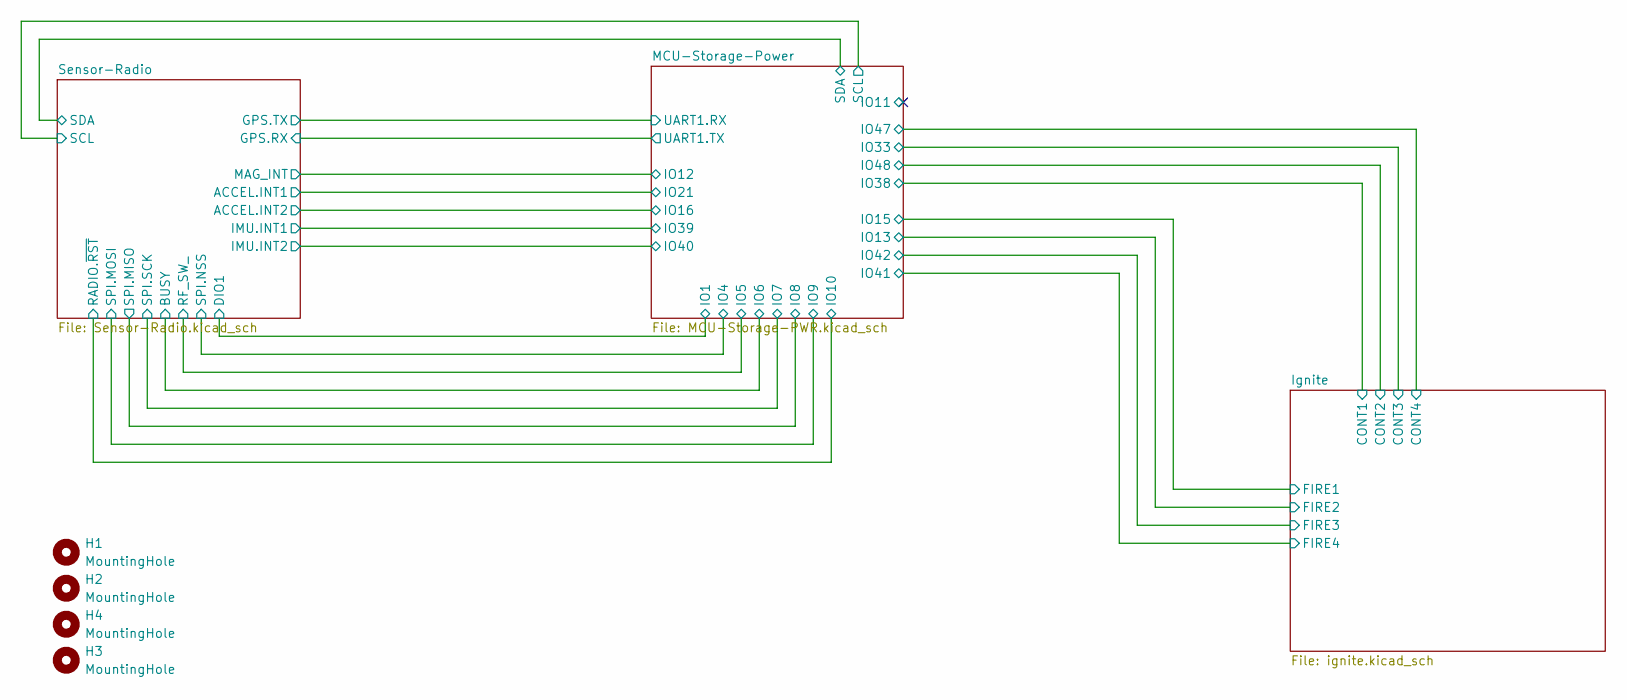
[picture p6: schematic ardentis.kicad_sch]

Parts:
H1, H2, H3, H4: MountingHole; MountingHole_3.5mm_Pad

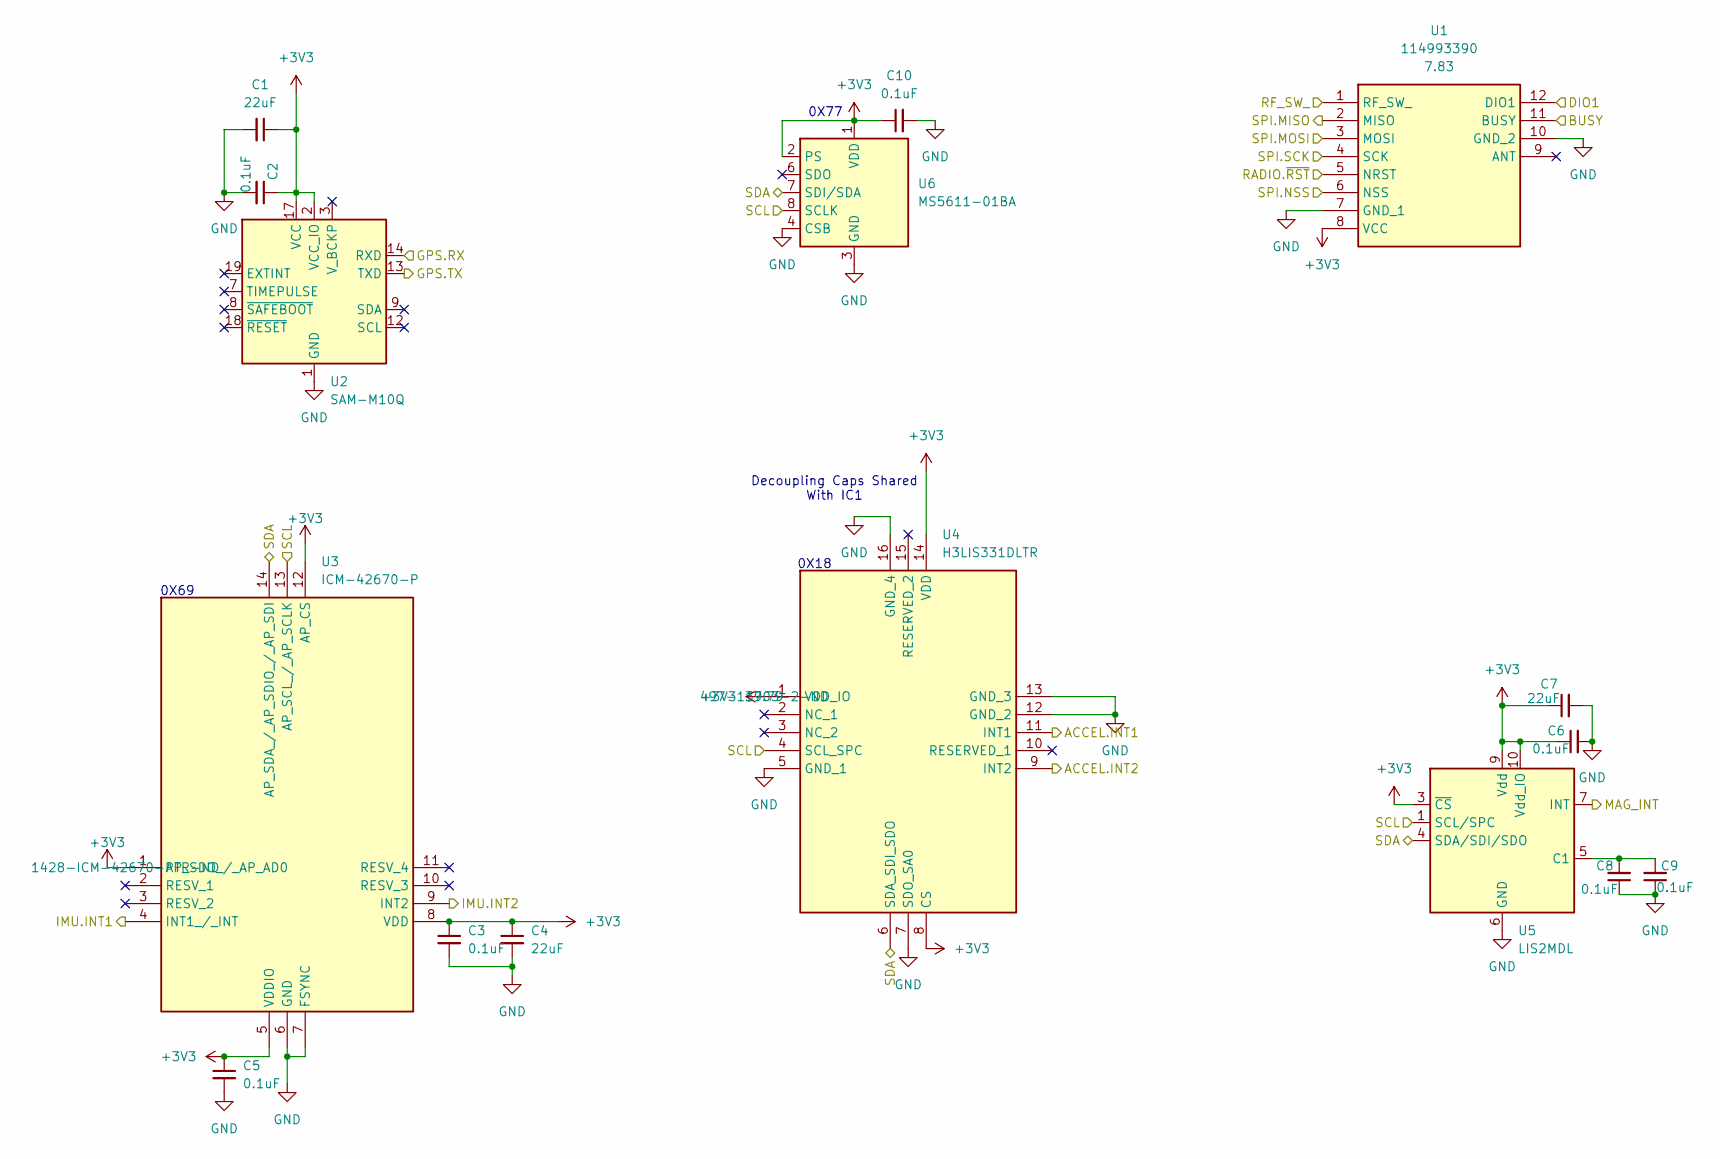
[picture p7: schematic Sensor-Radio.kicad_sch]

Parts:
C1, C4, C7: 22uF; C_0805_2012Metric_Pad1.18x1.45mm_HandSolder; Manufacturer_Part_Number CL21X226MQQNNNE; Mouser Part Number 81-GRM21BZ70J226ME4L
C2, C3, C5, C6, C8, C9, C10: 0.1uF; C_0805_2012Metric_Pad1.18x1.45mm_HandSolder; Manufacturer_Part_Number KGM21NR71H104KT; Mouser Part Number 581-08053C104K
U1: 114993390; Mouser Part Number 713-114993390
U2: SAM-M10Q; ublox_SAM-M10Q
U3: ICM-42670-P; ICM42670P; Mouser Part Number 410-ICM-42670-P
U4: H3LIS331DLTR; Mouser Part Number 511-H3LIS331DLTR
U5: LIS2MDL; LGA-12_2x2mm_P0.5mm; Manufacturer_Part_Number LIS2MDLTR
U6: MS5611-01BA; LGA-8_3x5mm_P1.25mm; Manufacturer_Part_Number MS561101BA03-50

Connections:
+3V3: C1.1, C2.1, C3.1, C4.1, C5.1, C6.1, C7.1, C10.1, U1.8 (VCC), U2.2 (VCC_IO), U2.17 (VCC), U3.1 (AP_SDO_/_AP_AD0), U3.5 (VDDIO), U3.8 (VDD), U3.12 (AP_CS), U4.1 (VDD_IO), U4.8 (CS), U4.14 (VDD), U5.3 (~CS), U5.9 (Vdd), U5.10 (Vdd_IO), U6.1 (VDD), U6.2 (PS); also elsewhere on the board
/MCU-Storage-Power/IO1: U1.12 (DIO1); also elsewhere on the board
/MCU-Storage-Power/IO4: U1.6 (NSS); also elsewhere on the board
/MCU-Storage-Power/IO5: U1.1 (RF_SW_); also elsewhere on the board
/MCU-Storage-Power/IO6: U1.11 (BUSY); also elsewhere on the board
/MCU-Storage-Power/IO7: U1.4 (SCK); also elsewhere on the board
/MCU-Storage-Power/IO8: U1.2 (MISO); also elsewhere on the board
/MCU-Storage-Power/IO9: U1.3 (MOSI); also elsewhere on the board
/MCU-Storage-Power/IO10: U1.5 (NRST); also elsewhere on the board
/MCU-Storage-Power/IO12: U5.7 (INT); also elsewhere on the board
/MCU-Storage-Power/IO16: U4.9 (INT2); also elsewhere on the board
/MCU-Storage-Power/IO21: U4.11 (INT1); also elsewhere on the board
/MCU-Storage-Power/IO39: U3.4 (INT1_/_INT); also elsewhere on the board
/MCU-Storage-Power/IO40: U3.9 (INT2); also elsewhere on the board
/MCU-Storage-Power/SCL: U3.13 (AP_SCL_/_AP_SCLK), U4.4 (SCL_SPC), U5.1 (SCL/SPC), U6.8 (SCLK); also elsewhere on the board
/MCU-Storage-Power/SDA: U3.14 (AP_SDA_/_AP_SDIO_/_AP_SDI), U4.6 (SDA_SDI_SDO), U5.4 (SDA/SDI/SDO), U6.7 (SDI/SDA); also elsewhere on the board
/MCU-Storage-Power/UART1.RX: U2.13 (TXD); also elsewhere on the board
/MCU-Storage-Power/UART1.TX: U2.14 (RXD); also elsewhere on the board
GND: C1.2, C2.2, C3.2, C4.2, C5.2, C6.2, C7.2, C8.1, C9.1, C10.2, U1.7 (GND_1), U1.10 (GND_2), U2.1 (GND), U2.4 (GND), U2.5 (GND), U2.6 (GND), U2.10 (GND), U2.11 (GND), U2.15 (GND), U2.16 (GND), U2.20 (GND), U3.6 (GND), U3.7 (FSYNC), U4.5 (GND_1), U4.7 (SDO_SA0), U4.12 (GND_2), U4.13 (GND_3), U4.16 (GND_4), U5.6 (GND), U5.8 (GND), U6.3 (GND), U6.4 (CSB), U6.5 (CSB); also elsewhere on the board
unnamed: C8.2, C9.2, U5.5 (C1)

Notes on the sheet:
0X69
0X18
0X77
Decoupling Caps Shared With IC1

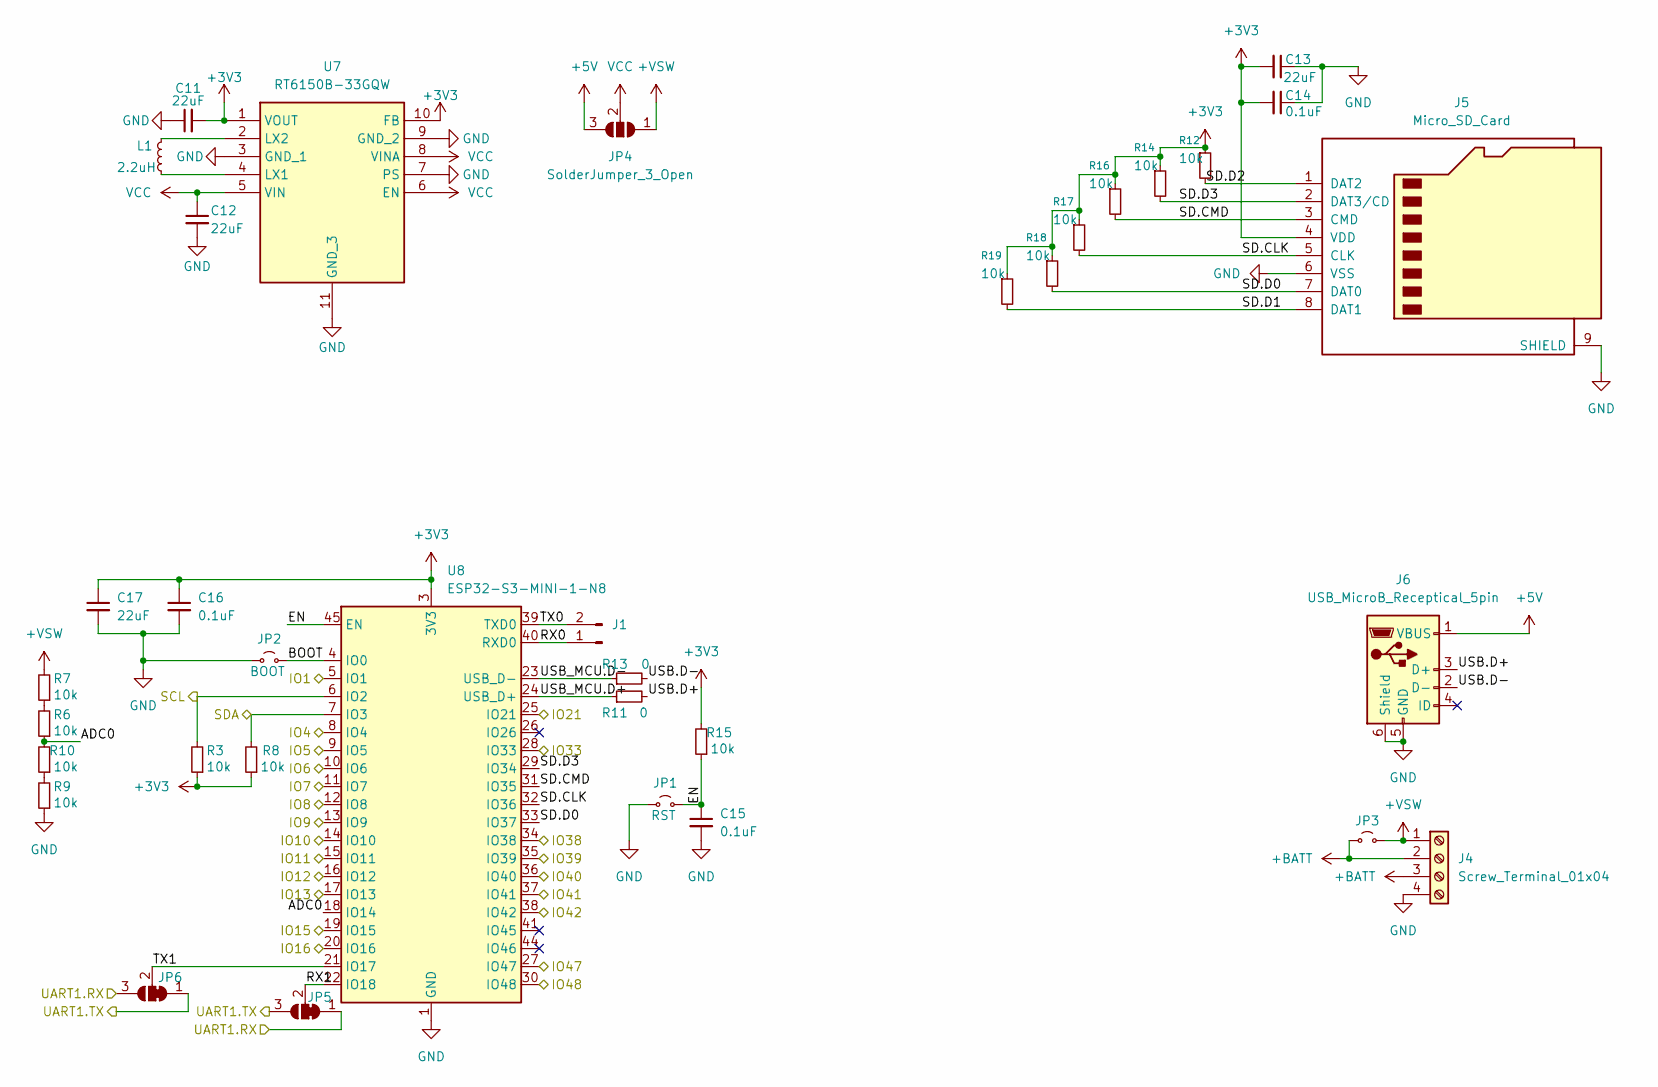
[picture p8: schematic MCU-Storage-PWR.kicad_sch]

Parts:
C11, C12, C13, C17: 22uF; C_0805_2012Metric_Pad1.18x1.45mm_HandSolder; Manufacturer_Part_Number CL21X226MQQNNNE; Mouser Part Number 81-GRM21BZ70J226ME4L
C14, C15, C16: 0.1uF; C_0805_2012Metric_Pad1.18x1.45mm_HandSolder; Manufacturer_Part_Number KGM21NR71H104KT; Mouser Part Number 581-08053C104K
J1: Conn_01x02_Pin; TestPoint_2Pads_Pitch2.54mm_Drill0.8mm
J4: Screw_Terminal_01x04; TB00150004BE; Manufacturer_Part_Number TB001-500-04BE
J5: Micro_SD_Card; MEM20670218000A; Manufacturer_Part_Number MEM2067-02-180-00-A; Mouser Part Number 640-MEM20670218000A
J6: USB_MicroB_Receptical_5pin; UJ2MIBHGSMTTR; Manufacturer_Part_Number UJ2-MIBH-G-SMT-TR; Mouser Part Number 490-UJ2-MIBH-G-SMTTR
JP1: RST; TestPoint_2Pads_Pitch2.54mm_Drill0.8mm
JP2: BOOT; TestPoint_2Pads_Pitch2.54mm_Drill0.8mm
JP3: Jumper_2_Small_Open; SolderJumper-2_P1.3mm_Open_TrianglePad1.0x1.5mm
JP4: SolderJumper_3_Open; SolderJumper-3_P2.0mm_Open_TrianglePad1.0x1.5mm
JP5, JP6: SolderJumper_3_Bridged12; SolderJumper-3_P2.0mm_Open_TrianglePad1.0x1.5mm
L1: 2.2uH; L_1008_2520Metric_Pad1.43x2.20mm_HandSolder; Manufacturer_Part_Number WIP252012S-2R2MLDG; Mouser Part Number 652-SRN2510F-2R2M
R3, R6, R7, R8, R9, R10, R12, R14, R15, R16, R17, R18, R19: 10k; R_0805_2012Metric_Pad1.20x1.40mm_HandSolder; Manufacturer_Part_Number RC0805JR-0710KL; Mouser Part Number 660-RK73B2ATTD103J
R11, R13: 0; R_0805_2012Metric_Pad1.20x1.40mm_HandSolder; Manufacturer_Part_Number ERJ-6GEY0R00V; Mouser Part Number 660-RK73Z2ATTD
U7: RT6150B-33GQW; SON50P250X250X80-11N-D; Mouser Part Number 835-RT6150B-33GQW
U8: ESP32-S3-MINI-1-N8; ESP32-S3-MINI-1; Manufacturer_Part_Number 1965-ESP32-S3-MINI-1-N4R2TR-ND; Mouser Part Number 356-ESP32-MINI1PH3Q0

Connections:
+3V3: C11.2, C13.2, C14.2, C16.1, C17.1, J5.4 (VDD), R3.1, R8.1, R12.1, R14.1, R15.2, R16.1, R17.1, R18.1, R19.1, U7.1 (VOUT), U7.10 (FB), U8.3 (3V3); also elsewhere on the board
+5V: J6.1 (VBUS), JP4.3 (B)
+BATT: J4.2, J4.3, JP3.1 (A)
+VSW: J4.1, JP3.2 (B), JP4.1 (A), R7.2; also elsewhere on the board
/Ignite/CONT1: U8.34 (IO38); also elsewhere on the board
/Ignite/CONT2: U8.30 (IO48); also elsewhere on the board
/Ignite/CONT3: U8.28 (IO33); also elsewhere on the board
/Ignite/CONT4: U8.27 (IO47); also elsewhere on the board
/Ignite/FIRE1: U8.19 (IO15); also elsewhere on the board
/Ignite/FIRE2: U8.17 (IO13); also elsewhere on the board
/Ignite/FIRE3: U8.38 (IO42); also elsewhere on the board
/Ignite/FIRE4: U8.37 (IO41); also elsewhere on the board
/MCU-Storage-Power/ADC0: R6.1, R10.2, U8.18 (IO14)
/MCU-Storage-Power/BOOT: JP2.2 (B), U8.4 (IO0)
/MCU-Storage-Power/EN: C15.1, JP1.2 (B), R15.1, U8.45 (EN)
/MCU-Storage-Power/IO1: U8.5 (IO1); also elsewhere on the board
/MCU-Storage-Power/IO4: U8.8 (IO4); also elsewhere on the board
/MCU-Storage-Power/IO5: U8.9 (IO5); also elsewhere on the board
/MCU-Storage-Power/IO6: U8.10 (IO6); also elsewhere on the board
/MCU-Storage-Power/IO7: U8.11 (IO7); also elsewhere on the board
/MCU-Storage-Power/IO8: U8.12 (IO8); also elsewhere on the board
/MCU-Storage-Power/IO9: U8.13 (IO9); also elsewhere on the board
/MCU-Storage-Power/IO10: U8.14 (IO10); also elsewhere on the board
/MCU-Storage-Power/IO11: U8.15 (IO11)
/MCU-Storage-Power/IO12: U8.16 (IO12); also elsewhere on the board
/MCU-Storage-Power/IO16: U8.20 (IO16); also elsewhere on the board
/MCU-Storage-Power/IO21: U8.25 (IO21); also elsewhere on the board
/MCU-Storage-Power/IO39: U8.35 (IO39); also elsewhere on the board
/MCU-Storage-Power/IO40: U8.36 (IO40); also elsewhere on the board
/MCU-Storage-Power/RX0: J1.1, U8.40 (RXD0)
/MCU-Storage-Power/RX1: JP5.2 (C), U8.22 (IO18)
/MCU-Storage-Power/SCL: R3.2, U8.6 (IO2); also elsewhere on the board
/MCU-Storage-Power/SD.CLK: J5.5 (CLK), R17.2, U8.32 (IO36)
/MCU-Storage-Power/SD.CMD: J5.3 (CMD), R16.2, U8.31 (IO35)
/MCU-Storage-Power/SD.D0: J5.7 (DAT0), R18.2, U8.33 (IO37)
/MCU-Storage-Power/SD.D1: J5.8 (DAT1), R19.2
/MCU-Storage-Power/SD.D2: J5.1 (DAT2), R12.2
/MCU-Storage-Power/SD.D3: J5.2 (DAT3/CD), R14.2, U8.29 (IO34)
/MCU-Storage-Power/SDA: R8.2, U8.7 (IO3); also elsewhere on the board
/MCU-Storage-Power/TX0: J1.2, U8.39 (TXD0)
/MCU-Storage-Power/TX1: JP6.2 (C), U8.21 (IO17)
/MCU-Storage-Power/UART1.RX: JP5.1 (A), JP6.3 (B); also elsewhere on the board
/MCU-Storage-Power/UART1.TX: JP5.3 (B), JP6.1 (A); also elsewhere on the board
/MCU-Storage-Power/USB.D+: J6.3 (D+), R11.2
/MCU-Storage-Power/USB.D-: J6.2 (D-), R13.2
/MCU-Storage-Power/USB_MCU.D+: R11.1, U8.24 (USB_D+)
/MCU-Storage-Power/USB_MCU.D-: R13.1, U8.23 (USB_D-)
GND: C11.1, C12.2, C13.1, C14.1, C15.2, C16.2, C17.2, J4.4, J5.6 (VSS), J5.9 (SHIELD), J6.5 (GND), J6.6 (Shield), JP1.1 (A), JP2.1 (A), R9.1, U7.3 (GND_1), U7.7 (PS), U7.9 (GND_2), U7.11 (GND_3), U8.1 (GND), U8.2 (GND), U8.42 (GND), U8.43 (GND), U8.46 (GND), U8.47 (GND), U8.48 (GND), U8.49 (GND), U8.50 (GND), U8.51 (GND), U8.52 (GND), U8.53 (GND), U8.54 (GND), U8.55 (GND), U8.56 (GND), U8.57 (GND), U8.58 (GND), U8.59 (GND), U8.60 (GND), U8.61 (GND), U8.62 (GND), U8.63 (GND), U8.64 (GND), U8.65 (GND); also elsewhere on the board
unnamed: R6.2, R7.1
unnamed: R9.2, R10.1
unnamed: L1.1, U7.4 (LX1)
unnamed: L1.2, U7.2 (LX2)
VCC: C12.1, JP4.2 (C), U7.5 (VIN), U7.6 (EN), U7.8 (VINA)

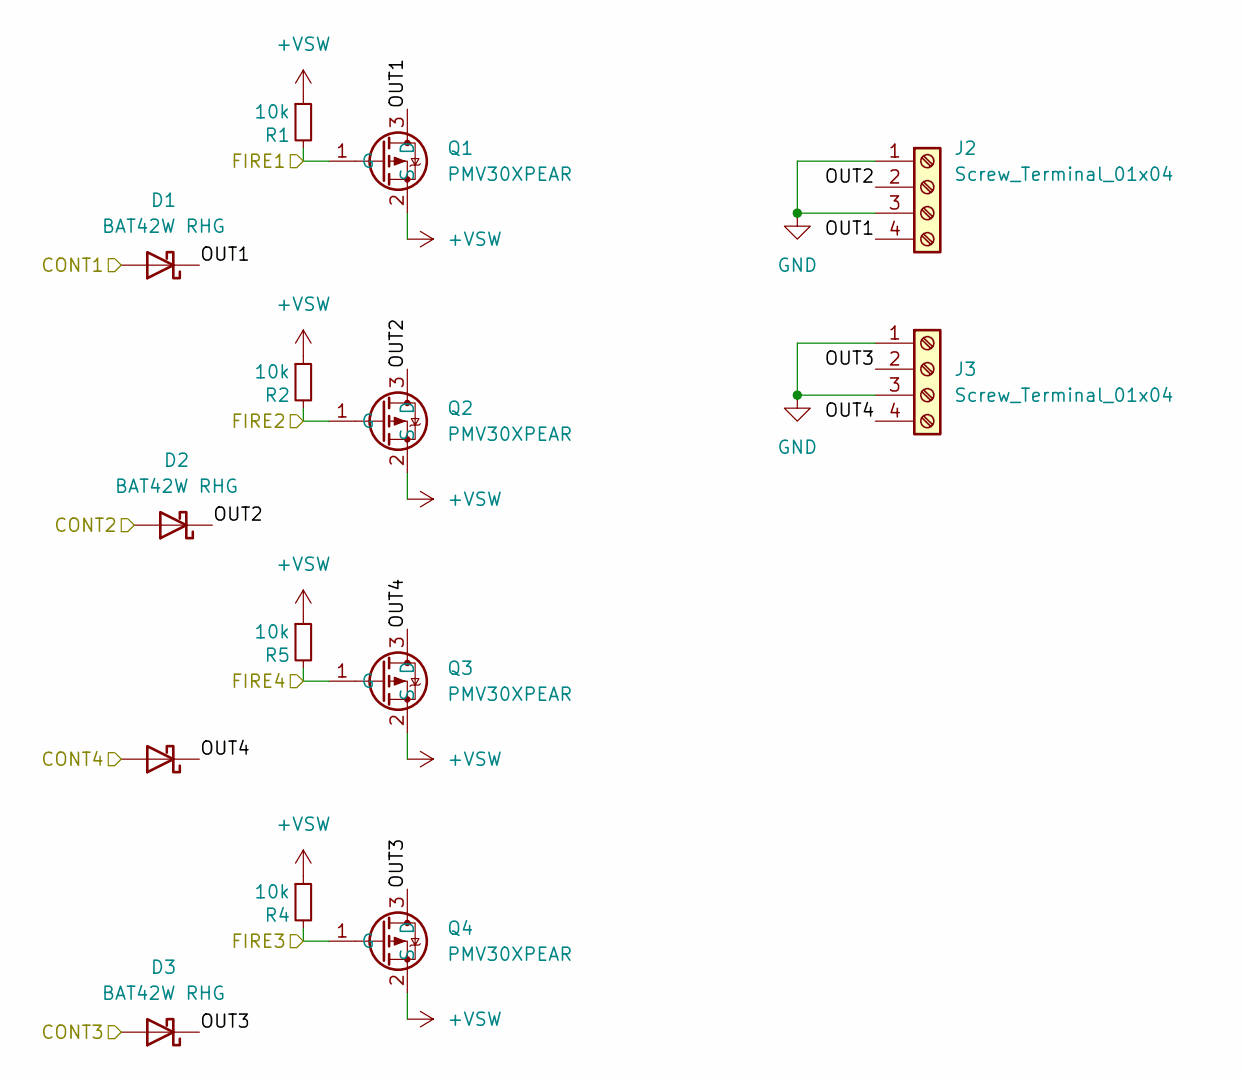
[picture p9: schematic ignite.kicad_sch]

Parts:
D1, D2, D3, D4: BAT42W RHG; D_SOD-123; Manufacturer_Part_Number BAT42W RHG
J2, J3: Screw_Terminal_01x04; TB00150004BE; Manufacturer_Part_Number TB001-500-04BE
Q1, Q2, Q3, Q4: PMV30XPEAR; SOT95P230X110-3N; Mouser Part Number 771-PMV30XPEAR
R1, R2, R4, R5: 10k; R_0805_2012Metric_Pad1.20x1.40mm_HandSolder; Manufacturer_Part_Number RC0805JR-0710KL; Mouser Part Number 660-RK73B2ATTD103J

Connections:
+VSW: Q1.2 (S), Q2.2 (S), Q3.2 (S), Q4.2 (S), R1.1, R2.1, R4.1, R5.1; also elsewhere on the board
/Ignite/CONT1: D1.2 (A); also elsewhere on the board
/Ignite/CONT2: D2.2 (A); also elsewhere on the board
/Ignite/CONT3: D3.2 (A); also elsewhere on the board
/Ignite/CONT4: D4.2 (A); also elsewhere on the board
/Ignite/FIRE1: Q1.1 (G), R1.2; also elsewhere on the board
/Ignite/FIRE2: Q2.1 (G), R2.2; also elsewhere on the board
/Ignite/FIRE3: Q4.1 (G), R4.2; also elsewhere on the board
/Ignite/FIRE4: Q3.1 (G), R5.2; also elsewhere on the board
/Ignite/OUT1: D1.1 (K), J2.4, Q1.3 (D)
/Ignite/OUT2: D2.1 (K), J2.2, Q2.3 (D)
/Ignite/OUT3: D3.1 (K), J3.2, Q4.3 (D)
/Ignite/OUT4: D4.1 (K), J3.4, Q3.3 (D)
GND: J2.1, J2.3, J3.1, J3.3; also elsewhere on the board

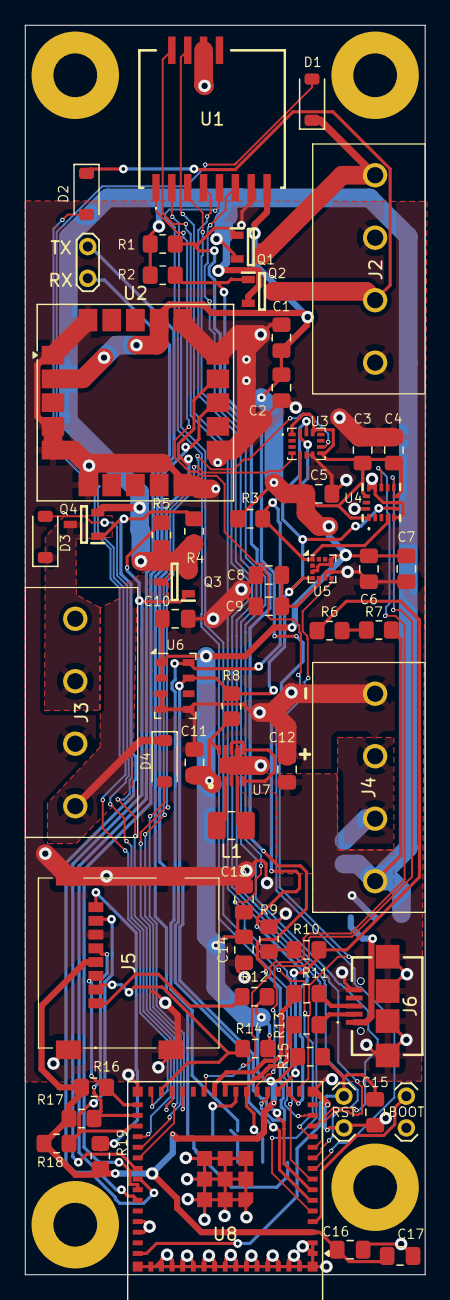
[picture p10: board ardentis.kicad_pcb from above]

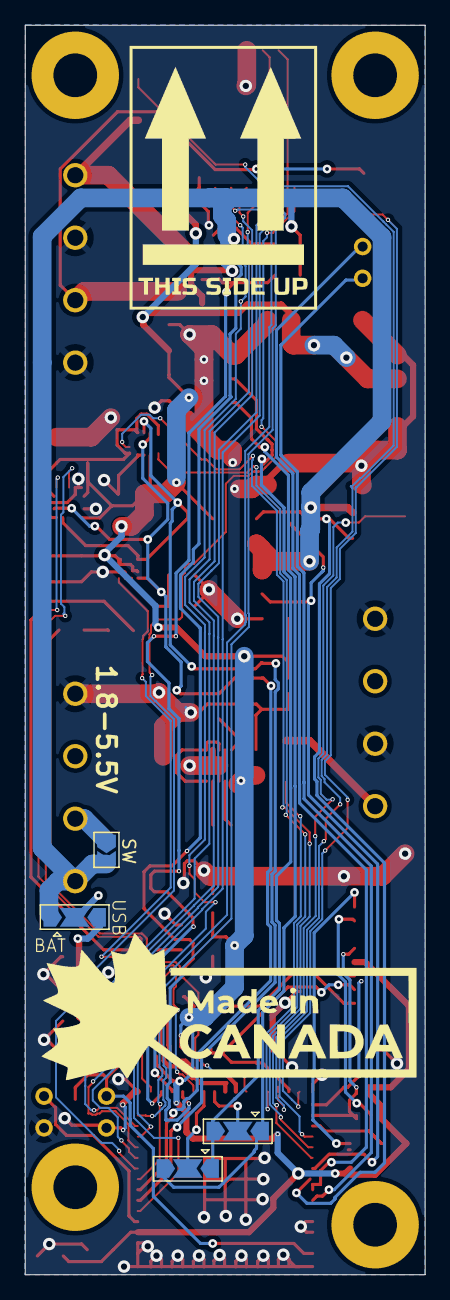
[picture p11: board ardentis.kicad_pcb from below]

Board: 2 copper layers, 32.0 x 100.0 mm, 69 parts (4 on the bottom side), 57 nets.

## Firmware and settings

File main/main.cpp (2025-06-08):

/** 
 * @file main.cpp
 * @author Roland Neill
 * @brief Main file for the Ardentis flight computer code.
 * @version 0.1-alpha
 * @date 2025-04-25
 * 
 * @copyright Copyright (c) 2025
 * 
 * @page main
 */
#include "pins.h"
#include "fire_modes.hpp"

#include "RadioParameters.h"

#include "ard_radio.h"

ard_RadioConfig_t radioConfig = {
  	ARD_RADIO_FREQ,
  	ARD_LORA_BW,
  	ARD_LORA_SF,
	ARD_LORA_CR,
  	ARD_LORA_SYNCWORD,
  	ARD_RADIO_TX_PWR
};
ard_RadioPins_t radioPins = {
  	ARD_RADIO_NSS,
  	ARD_RADIO_BUSY,
  	ARD_RADIO_NRST,
  	ARD_RADIO_DIO1,
  	ARD_RADIO_SPI_MISO,
  	ARD_RADIO_SPI_MOSI,
  	ARD_RADIO_SPI_SCK
};

ardRadio radio(radioPins);

#include "data_struct.h"

#include "ard_deployment.h"


#include "ard_log.h"

const char* main_TAG = "Main";

ardLog main_log(main_TAG);

void txCallback(void) {
  	// Callback function for when the radio is done transmitting
  	radio.doneTX();
}

#include <Arduino.h>
#include <Wire.h>

#include <FS.h>
#include <LittleFS.h>

#include <SD.h>

#include <Preferences.h>

#include "ard_sensor.h"

ardSensors sensors(ARD_SDA, ARD_SCL, 1, ARD_GPS_UART, ARD_GPS_TX, ARD_GPS_RX);


File flightLog;

bool fire_signal_1 = false;
bool fire_signal_2 = false;
bool fire_signal_3 = false;
bool fire_signal_4 = false;

bool continuity_1 = false;
bool continuity_2 = false;
bool continuity_3 = false;
bool continuity_4 = false;

bool apogee = false; // Set to true when apogee is detected
uint16_t time_since_apogee = 0; // Set to true when time since apogee is detected
uint16_t altitude = 0;
bool descending = false; // Set to true when descending is detected
bool ascending = false; // Set to true when ascending is detected
uint16_t time_since_liftoff = 0;

// TODO: Change these parameters to read from preferences when implemented
int ref_pressure = 101325; // Sea level pressure in Pa

uint8_t fire_1_mode = ARD_FIRE_INACTIVE;
uint8_t fire_1_param = 0; // Parameter for fire_1_mode. Meaning depends on mode selected.
uint8_t fire_2_mode = ARD_FIRE_INACTIVE;
uint8_t fire_2_param = 0; // Parameter for fire_2_mode. Meaning depends on mode selected.
uint8_t fire_3_mode = ARD_FIRE_INACTIVE;
uint8_t fire_3_param = 0; // Parameter for fire_3_mode. Meaning depends on mode selected.
uint8_t fire_4_mode = ARD_FIRE_INACTIVE;
uint8_t fire_4_param = 0; // Parameter for fire_4_mode. Meaning depends on mode selected.

uint8_t fire_1_altitude = 0; // in meters
uint8_t fire_2_altitude = 0; // in meters
uint8_t fire_3_altitude = 0; // in meters
uint8_t fire_4_altitude = 0; // in meters


void setup(void) {
  	Serial.begin(115200);
  	while (!Serial) delay(10);

	radio.begin(radioConfig);
	radio.setTxInt(txCallback);

  	if (sensors.initSensors(0x18, 0x68, 0x77, ARD_GPS_BAUD) != ERROR_NONE) {
		main_log.error("Sensor initialization failed.");
  	} else {
		main_log.info("Sensor initialization successful.");
  	}


  	// SD Card Setup
  	if (!SD.begin(4)) {
		Serial.println("[ERROR] SD initialization failed!");
		while (1);
  	}
  	Serial.println("[SD] initialization done.");

  	flightLog = SD.open("flight.log", FILE_WRITE);
  	if (flightLog) {
		Serial.print("[SD] Writing to flight.log...");
		flightLog.println("testing 1, 2, 3.");
		// close the file:
		flightLog.close();
		Serial.println("[SD] Done writing to flight.log");
  	} else {
		// if the file didn't open, print an error:
		Serial.println("[ERROR] Error opening flight.log");

  	}

  	// Initialize Fire Output GPIOs
  	pinMode(ARD_FIRE1, OUTPUT);
  	digitalWrite(ARD_FIRE1, HIGH);
  	pinMode(ARD_FIRE2, OUTPUT);
  	digitalWrite(ARD_FIRE2, HIGH);
  	pinMode(ARD_FIRE3, OUTPUT);
  	digitalWrite(ARD_FIRE3, HIGH);
  	pinMode(ARD_FIRE4, OUTPUT);
  	digitalWrite(ARD_FIRE4, HIGH);

  	pinMode(ARD_CONT1, INPUT_PULLUP);
  	pinMode(ARD_CONT2, INPUT_PULLUP);
  	pinMode(ARD_CONT3, INPUT_PULLUP);
  	pinMode(ARD_CONT4, INPUT_PULLUP);

  	Serial.println("[OUTPUT] Output GPIOs initialized.");

	}

void loop() {

  	ArdDataStruct data;
  
  	sensors.update();



  	// Check Continuity
  	data.cont1 = digitalRead(ARD_CONT1);
  	data.cont2 = digitalRead(ARD_CONT2);
  	data.cont3 = digitalRead(ARD_CONT3);
  	data.cont4 = digitalRead(ARD_CONT4);


  	for (int i = 1; i <= 4; i++) {
		uint8_t fire_mode = 0;
		uint16_t fire_param = 0;
		bool* fire_signal = nullptr;
		bool* data_signal = nullptr;

		switch (i) {
	  	case 1:
			fire_mode = fire_1_mode;
			fire_param = fire_1_param;
			fire_signal = &fire_signal_1;
			data_signal = &data.fired_1;
			break;
	  	case 2:
			fire_mode = fire_2_mode;
			fire_param = fire_2_param;
			fire_signal = &fire_signal_2;
			data_signal = &data.fired_2;
			break;
		case 3:
			fire_mode = fire_3_mode;
			fire_param = fire_3_param;
			fire_signal = &fire_signal_3;
			data_signal = &data.fired_3;
			break;
		case 4:
			fire_mode = fire_4_mode;
			fire_param = fire_4_param;
			fire_signal = &fire_signal_4;
			data_signal = &data.fired_4;
			break;
		}
		// Check if the fire mode is active
		if (fire_mode == 1) { // Fire at apogee
			if (apogee == true && time_since_apogee > fire_param) {
				*fire_signal = true;
				*data_signal = true;
			} else {
				*fire_signal = false;
			}
		} else if (fire_mode == 2) { // Fire at or below set altitude on descent
			*fire_signal = (altitude <= fire_param) && (descending == true);
		} else if (fire_mode == 3) { // Fire at or above set altitude on ascent
			*fire_signal = (altitude >= fire_param) && (ascending == true);
		} else if (fire_mode == 4) { // Fire at set time after liftoff
			*fire_signal = time_since_apogee > fire_param;
		} else {
			*fire_signal = false;
		}
  	}

	if (!radio.busy) {
		RadioPacket radioPacket;
		strncpy(radioPacket.callsign, "VE3FSZ", sizeof(radioPacket.callsign) - 1);
		radioPacket.callsign[sizeof(radioPacket.callsign) - 1] = '\0';
		radioPacket.latitude = data.latitude;
		radioPacket.longitude = data.longitude;
		radioPacket.altitude = data.altitude;

		radio.sendData(radioPacket);


  		Serial.println(F("[RADIO] Sending packet"));

		if (fire_signal_1) {
			Serial.println("[OUTPUT] Firing Output 1.");
			digitalWrite(ARD_FIRE1, LOW);
			delay(1000);
			digitalWrite(ARD_FIRE1, HIGH);
		}
	}
}

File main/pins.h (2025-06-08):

#define ARD_RADIO_SPI_SCK (gpio_num_t)7
#define ARD_RADIO_SPI_MISO (gpio_num_t)8
#define ARD_RADIO_SPI_MOSI (gpio_num_t)9
#define ARD_RADIO_NSS (gpio_num_t)4
#define ARD_RADIO_DIO1 (gpio_num_t)1
#define ARD_RADIO_NRST (gpio_num_t)10
#define ARD_RADIO_BUSY (gpio_num_t)6

#define ARD_GPS_RX gpio_num_t(17)
#define ARD_GPS_TX gpio_num_t(18)
#define ARD_GPS_UART 1U
#define ARD_GPS_BAUD 38400

#define ARD_SDA gpio_num_t(3)
#define ARD_SCL gpio_num_t(2)

#define ARD_IS33_INT1 gpio_num_t(21)
#define ARD_LIS33_INT2 gpio_num_t(16)

#define ARD_LIS2_INT gpio_num_t(12)
#define ARD_ICM_INT1 gpio_num_t(39)
#define ARD_ICM_INT2 gpio_num_t(40)

#define ARD_FIRE1 gpio_num_t(15)
#define ARD_FIRE2 gpio_num_t(13)
#define ARD_FIRE3 gpio_num_t(42)
#define ARD_FIRE4 gpio_num_t(41)

#define ARD_CONT1 14
#define ARD_CONT2 11
#define ARD_CONT3 43
#define ARD_CONT4 44

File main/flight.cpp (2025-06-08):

#ifdef FLIGHT
#include "pins.hpp"
#include "fire_modes.hpp"

#include "RadioParameters.h"

#include "ard_radio_packet_spec.h"
#include "data_struct.cpp"

#include <Arduino.h>
#include <Wire.h>

#include <FS.h>
#include <LittleFS.h>

#include <ICM42670P.h>

#include <SPI.h>
#include <SD.h>


#include <RadioLib.h>

//#include <SparkFun_LIS331.h>
#include <MS5611.h>

#include <Preferences.h>

#include <SparkFun_u-blox_GNSS_v3.h>

HardwareSerial gpsUART(ARD_GPS_UART);

SFE_UBLOX_GNSS_SERIAL gps;

File flightLog;

SX1262 radio = new Module(ARD_RADIO_NSS, ARD_RADIO_BUSY, ARD_RADIO_NRST, ARD_RADIO_DIO1);

MS5611 barometer(0x77);

bool fire_signal_1 = false;
bool fire_signal_2 = false;
bool fire_signal_3 = false;
bool fire_signal_4 = false;

bool continuity_1 = false;
bool continuity_2 = false;
bool continuity_3 = false;
bool continuity_4 = false;

bool apogee = false; // Set to true when apogee is detected
uint16_t time_since_apogee = 0; // Set to true when time since apogee is detected
uint16_t altitude = 0;
bool descending = false; // Set to true when descending is detected
bool ascending = false; // Set to true when ascending is detected
uint16_t time_since_liftoff = 0;

uint16_t ref_pressure = 101325U; // Sea level pressure in Pa

uint8_t fire_1_mode = ARD_FIRE_INACTIVE;
uint8_t fire_1_param = 0; // Parameter for fire_1_mode. Meaning depends on mode selected.
uint8_t fire_2_mode = ARD_FIRE_INACTIVE;
uint8_t fire_2_param = 0; // Parameter for fire_2_mode. Meaning depends on mode selected.
uint8_t fire_3_mode = ARD_FIRE_INACTIVE;
uint8_t fire_3_param = 0; // Parameter for fire_3_mode. Meaning depends on mode selected.
uint8_t fire_4_mode = ARD_FIRE_INACTIVE;
uint8_t fire_4_param = 0; // Parameter for fire_4_mode. Meaning depends on mode selected.

uint8_t fire_1_altitude = 0; // in meters
uint8_t fire_2_altitude = 0; // in meters
uint8_t fire_3_altitude = 0; // in meters
uint8_t fire_4_altitude = 0; // in meters


void setup(void) {
  Serial.begin(115200);
  while (!Serial) delay(10);

  gpsUART.begin(ARD_GPS_BAUD, SERIAL_8N1, ARD_GPS_RX, ARD_GPS_TX); // RX, TX

  gps.begin(gpsUART);

  gps.setNavigationFrequency(25);

  Wire.begin(ARD_SDA, ARD_SCL);
  if (barometer.begin() == true)
  {
    Serial.print("[BARO] MS5611 found at: ");
    Serial.println(barometer.getAddress());
  }
  else
  {
    Serial.println("[ERROR] MS5611 not found. halt.");
  }



  // initialize radio
  Serial.print(F("[RADIO] Initializing..."));
  uint16_t state = radio.begin(FREQ, BANDWIDTH, SF, CR, LoRa_SYNCWORD, RADIO_TX_PWR);
  if(state == RADIOLIB_ERR_NONE) {
    Serial.println(F("[RADIO] Initialization successful!"));
  } else {
    Serial.print(F("[ERROR] RADIO failed to initialize. Error code: "));
    Serial.println(state);
  }


  if (!SD.begin(4)) {
    Serial.println("[ERROR] SD initialization failed!");
    while (1);
  }
  Serial.println("[SD] initialization done.");

  flightLog = SD.open("flight.log", FILE_WRITE);
  if (flightLog) {
    Serial.print("[SD] Writing to flight.log...");
    flightLog.println("testing 1, 2, 3.");
    // close the file:
    flightLog.close();
    Serial.println("[SD] Done writing to flight.log");
  } else {
    // if the file didn't open, print an error:
    Serial.println("[ERROR] Error opening flight.log");

  }

  // Initialize Fire Output GPIOs
  pinMode(ARD_FIRE1, OUTPUT);
  digitalWrite(ARD_FIRE1, HIGH);
  pinMode(ARD_FIRE2, OUTPUT);
  digitalWrite(ARD_FIRE2, HIGH);
  pinMode(ARD_FIRE3, OUTPUT);
  digitalWrite(ARD_FIRE3, HIGH);
  pinMode(ARD_FIRE4, OUTPUT);
  digitalWrite(ARD_FIRE4, HIGH);

  pinMode(ARD_CONT1, INPUT_PULLUP);
  pinMode(ARD_CONT2, INPUT_PULLUP);
  pinMode(ARD_CONT3, INPUT_PULLUP);
  pinMode(ARD_CONT4, INPUT_PULLUP);

  Serial.println("[OUTPUT] Output GPIOs initialized.");

}

void loop() {

  ArdDataStruct data;

  // Check Continuity
  continuity_1 = digitalRead(ARD_CONT1);
  continuity_2 = digitalRead(ARD_CONT2);
  continuity_3 = digitalRead(ARD_CONT3);
  continuity_4 = digitalRead(ARD_CONT4);

  if(gps.getPVT() == true) {
    Serial.print("Latitude= "); Serial.print(gps.getLatitude() * 10e7, 6); Serial.print(" Longitude= "); Serial.println(gps.getLongitude() * 10e7, 6);
    Serial.print("Altitude= "); Serial.print(gps.getAltitude() * 1000, 6); Serial.println(" m");
    Serial.print("Horizontal Accuracy= "); Serial.println(gps.getHorizontalAccuracy() * 1000, 6); Serial.println(" m");
    Serial.print("Vertical Accuracy= "); Serial.println(gps.getVerticalAccuracy() * 1000, 6); Serial.println(" m");
    Serial.print("Date= "); Serial.print(gps.getDay()); Serial.print("/"); Serial.print(gps.getMonth()); Serial.print("/"); Serial.println(gps.getYear());
    Serial.print("Time= "); Serial.print(gps.getHour()); Serial.print(":"); Serial.print(gps.getMinute()); Serial.print(":"); Serial.println(gps.getSecond());
  }

  barometer.read();
  data.pressure = barometer.getPressure() * 100;
  data.temperature = barometer.getTemperature();
  data.latitude = gps.getLatitude() * 10e7; // Convert latitude to degrees
  data.longitude = gps.getLongitude() * 10e7; // Convert longitude to degrees


  for (int i = 1; i <= 4; i++) {
    uint8_t fire_mode = 0;
    uint16_t fire_param = 0;
    bool* fire_signal = nullptr;

    switch (i) {
      case 1:
        fire_mode = fire_1_mode;
        fire_param = fire_1_param;
        fire_signal = &fire_signal_1;
        break;
      case 2:
        fire_mode = fire_2_mode;
        fire_param = fire_2_param;
        fire_signal = &fire_signal_2;
        break;
      case 3:
        fire_mode = fire_3_mode;
        fire_param = fire_3_param;
        fire_signal = &fire_signal_3;
        break;
      case 4:
        fire_mode = fire_4_mode;
        fire_param = fire_4_param;
        fire_signal = &fire_signal_4;
        break;
    }

    if (fire_mode == 1) { // Fire at apogee
      *fire_signal = (apogee == true) && (time_since_apogee > fire_param);
    } else if (fire_mode == 2) { // Fire at or below set altitude on descent
      *fire_signal = (altitude <= fire_param) && (descending == true);
    } else if (fire_mode == 3) { // Fire at or above set altitude on ascent
      *fire_signal = (altitude >= fire_param) && (ascending == true);
    } else if (fire_mode == 4) { // Fire at set time after liftoff
      *fire_signal = time_since_apogee > fire_param;
    } else {
      *fire_signal = false;
    }
  }
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

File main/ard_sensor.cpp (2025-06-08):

#include "ard_sensor.h"

#include "ard_log.h"

const char* sensor_TAG = "Sensors";

ardLog sensor_log(sensor_TAG);

#include <esp_err.h>

#include <esp_timer.h>

#include <Wire.h>

#include <Arduino.h>
#include <stdint.h>

#include <ICM42670P.h>

#include <MS5611.h>

#include <Adafruit_Sensor.h> //Needed for adafruit sensor libraries
#include <Adafruit_H3LIS331.h> // For H3LIS331 High G Accelerometer

static const char* TAG = "Sensors";

void updateArdDataField(ardDataField* field, int16_t val) {
    field->val = val;
    field->timestamp = esp_timer_get_time(); // Timestamp in microseconds
    field->updated = true;
}

ardSensors::ardSensors(gpio_num_t sda, gpio_num_t scl, int i2c, int gps_uart_num, gpio_num_t gps_tx, gpio_num_t gps_rx) {
    gps_uart = HardwareSerial(gps_uart_num); // Initialize the GPS UART serial port

    sda = sda; // Assign the SDA pin
    scl = scl; // Assign the SCL pin

    uart_rx = gps_rx; // Assign the GPS RX pin
    uart_tx = gps_tx; // Assign the GPS TX pin

    const i2c_master_bus_config_t i2c_bus_config = {
        .i2c_port = i2c,
        .sda_io_num = sda,
        .scl_io_num = scl,
        .clk_source = I2C_CLK_SRC_DEFAULT,
    };

    esp_err_t ret = i2c_new_master_bus(&i2c_bus_config, &i2c_handle);

    ard_sensor_i2c = TwoWire(i2c); // Initialize I2C with the specified I2C number
}

ardSensors::~ardSensors() {
    icm42670_delete(imu_handle); // Delete the ICM42670 handle
}

esp_err_t ardSensors::initSensors(int LIS331_addr, int imu_adr, int baro_addr, int gps_baud) {
    esp_err_t ret = ESP_OK;

    ard_sensor_i2c.begin(sda, scl);

    gps_uart.begin(gps_baud, SERIAL_8N1, uart_rx, uart_tx);

    if (icm42670_create(i2c_handle, imu_adr, &imu_handle) != 0) {
        sensor_log.warn("ICM42670 initialization failed.");
        ret = ESP_FAIL;
    } else {
        sensor_log.info("ICM42670 initialized successfully.");
    }

    const icm42670_cfg_t imu_cfg = {
        .acce_fs = ACCE_FS_16G,
        .acce_odr = ACCE_ODR_100HZ,
        .gyro_fs = GYRO_FS_2000DPS,
        .gyro_odr = GYRO_ODR_100HZ,
    };

    if (icm42670_config(imu_handle, &imu_cfg) != 0) {
        sensor_log.warn("ICM42670 configuration failed.");
        ret = ESP_FAIL;
    } else {
        sensor_log.info("ICM42670 configured successfully.");
    }

    if (icm42670_acce_set_pwr(imu_handle, ACCE_PWR_LOWNOISE) != 0) {
        sensor_log.warn("Error initializing ICM42670 accelerometer.");
        ret = ESP_FAIL;
    } else {
        sensor_log.info("ICM42670 accelerometer initialized successfully.");
    }

    if (icm42670_gyro_set_pwr(imu_handle, GYRO_PWR_LOWNOISE) != 0) {
        sensor_log.warn("Error initializing ICM42670 gyro.");
        ret = ESP_FAIL;
    } else {
        sensor_log.info("ICM42670 gyro initialized successfully.");
    }

    if (accel.begin_I2C(LIS331_addr, &ard_sensor_i2c) != 0) {
        sensor_log.warn("Could not start H3LIS331 accelerometer.");
        ret = ESP_FAIL;
    } else {
        sensor_log.info("H3LIS331 accelerometer started successfully.");
    }

    accel.setRange(H3LIS331_RANGE_400_G);

    accel.setDataRate(LIS331_DATARATE_100_HZ);

    barometer = MS5611(baro_addr, &ard_sensor_i2c); // MS5611 address
    barometer.begin();

    if (gps.begin(gps_uart) != 0) {
        sensor_log.warn("GPS initialization failed.");
        ret = ESP_FAIL;
    } else {
        sensor_log.info("GPS initialized successfully.");
        gps.setNavigationFrequency(25);
    }

    return ret;
}
// Function to update the sensor data
esp_err_t ardSensors::update() {
    esp_err_t ret = ESP_OK;

    if (esp_timer_get_time() - imu_update_time >= imu_update_interval) {

        icm42670_value_t accel_value;
        if (icm42670_get_acce_value(imu_handle, &accel_value) != 0) {
            sensor_log.warn("Error reading ICM42670 accelerometer.");
            ret = ESP_FAIL;
        } else {
            sensor_log.verb("ICM42670 accelerometer read successfully.");

            updateArdDataField(&accelX, accel_value.x); // Check units when have hardware
            updateArdDataField(&accelY, accel_value.y); // Check units when have hardware
            updateArdDataField(&accelZ, accel_value.z); // Check units when have hardware
        }

        icm42670_value_t gyro_value;
        if (icm42670_get_gyro_value(imu_handle, &gyro_value) != 0) {
            sensor_log.warn("Error reading ICM42670 gyro.");
            ret = ESP_FAIL;
        } else {
            sensor_log.verb("ICM42670 gyro read successfully.");

            updateArdDataField(&gyroX, gyro_value.x); // Check units when have hardware
            updateArdDataField(&gyroY, gyro_value.y); // Check units when have hardware
            updateArdDataField(&gyroZ, gyro_value.z); // Check units when have hardware
        }

        imu_update_time = esp_timer_get_time(); // Timestamp in microseconds
    }

    // Read High G Accelerometer Data
    if (esp_timer_get_time() - high_g_accel_update_time >= high_g_accel_update_interval) {
        sensors_event_t accel_event;
        accel.getEvent(&accel_event);

        updateArdDataField(&highAccelX, accel_event.acceleration.x); // In m/s^2
        updateArdDataField(&highAccelY, accel_event.acceleration.y); // In m/s^2
        updateArdDataField(&highAccelZ, accel_event.acceleration.z); // In m/s^2

        high_g_accel_update_time = esp_timer_get_time(); // Timestamp in microseconds
    }

    if (esp_timer_get_time() - barometer_update_time >= barometer_update_interval) {
        barometer.read(); // Read the barometer data

        updateArdDataField(&pressure, barometer.getPressure() * 100); // Convert to Pa
        updateArdDataField(&temperature, barometer.getTemperature()); // In degrees Celsius

        barometer_update_time = esp_timer_get_time(); // Timestamp in microseconds
    }

    if (esp_timer_get_time() - gps_update_time >= gps_update_interval) {
        if (gps.getPVT() == true) {
            updateArdDataField(&latitude, gps.getLatitude() * 10e7); // Convert to degrees
            updateArdDataField(&longitude, gps.getLongitude() * 10e7); // Convert to degrees
            updateArdDataField(&horizAccuracy, gps.getHorizontalAccuracy() * 1000); // Convert to meters
            updateArdDataField(&vertAccuracy, gps.getVerticalAccuracy() * 1000); // Convert to meters
            updateArdDataField(&gps_altitude, gps.getAltitude() * 1000); // Convert to meters

            gps_update_time = esp_timer_get_time(); // Timestamp in microseconds
        }
    }

    return ret;
} 

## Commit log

2025-04-09 Initial Design
    Initial Schematic Design
    [MCU-Storage-PWR.kicad_sch, Power.kicad_sch, Sensor-Radio.kicad_sch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]
2025-06-08 Initial code
    Initial code. Theoretically will work but not tested due to lack of hardware and updates to PCB.
    [BOM.xlsx, MCU-Storage-PWR.kicad_sch, Pro.kicad_sch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]
